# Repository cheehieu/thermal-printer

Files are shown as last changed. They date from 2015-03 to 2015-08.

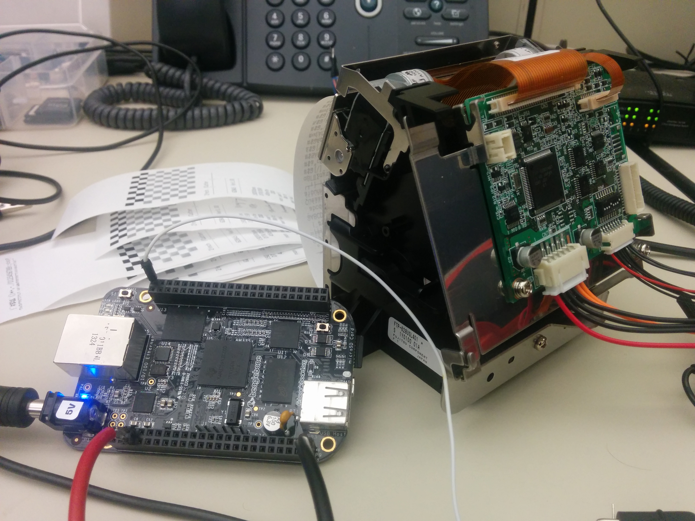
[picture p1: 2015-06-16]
images/printer_prototype.jpg

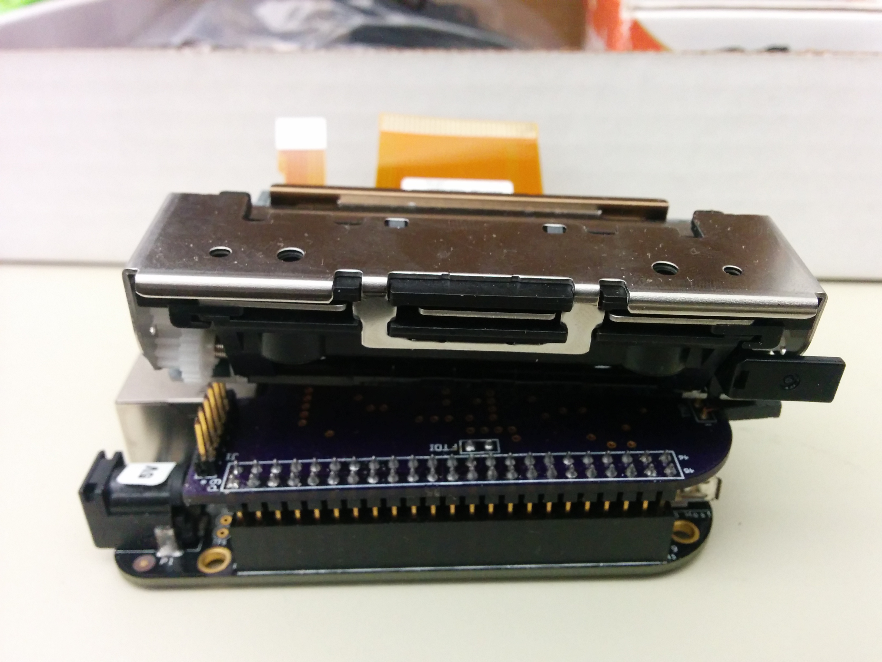
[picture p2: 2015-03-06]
images/print_head.jpg

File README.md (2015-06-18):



## Overview
This project is a thermal printer reference design featuring the PRU-ICSS on the AM335x. It was inspired by a similar project by [Andreas Dannenberg](https://gitorious.design.ti.com/pruprinter), who prototyped a functioning thermal printer out of a gutted POS unit and a BeagleBone Black. Here is a video of his prototype: [https://youtu.be/tVr5VrtNZiQ].

The main intent of this project is to showcase the real-time abilities of the PRU-ICSS for time-sensitive motor control applications. It also serves as a platform to demonstrate the new Linux-PRU software communication interface, . Much of this project's design follows Andreas' design choices (TI components, area- and cost-sensitive), but also incorporates some ideas from the FTP-628DSL491R interface board, which is an EVM for the Fujitsu FTP-628MCL401 print head.

## Hardware


### BeagleBone Black
The AM335x processor on the BeagleBone Black contains the Programmable Real-Time Unit and Industrial Communication Sub System (PRU-ICSS). The PRU consists of dual 32-bit RISC cores, which operate at 200MHz single cycle and have direct access to general IO. This allows for 100% predictable timing, making the PRU an excellent solution for thermal strobes and motor control. 

In this project, the PRU is designed to handle the print head logic and motor control for both head and cutter stepper motors. I tried to choose logical PRU signal groupings to simplify board layout and software design. Make sure to execute the proper pin-mux changes in the device tree. The PRU signals are connected on the cape as follows:

| BBB Pin |  PRU Signal | Cape Function |
|:---:|:---:|:---:|
| P8.30 | pru1_r30_11 | Vdd supply enable |
| P8.21 | pru1_r30_12 | VH supply enable |
| P8.20 | pru1_r30_13 | Buffer output enable |
| P8.15 | pru0_r31_15 | Motor driver fault HEAD |
| P9.26 | pru1_r31_16 | Motor driver fault CUT  |
| P8.46 | pru1_r30_1  | MTAn_head |
| P8.45 | pru1_r30_0  | MTA_head |
| P8.43 | pru1_r30_2  | MTBn_head |
| P8.44 | pru1_r30_3  | MTB_head |
| P8.41 | pru1_r30_4  | MTA_cut |
| P8.42 | pru1_r30_5  | MTAn_cut |
| P8.39 | pru1_r30_6  | MTB_cut |
| P8.40 | pru1_r30_7  | MTBn_cut |
| P9.31 | pru0_r30_0  | STB1 |
| P9.29 | pru0_r30_1  | STB2 |
| P9.30 | pru0_r30_2  | STB3 |
| P9.28 | pru0_r30_3  | STB4 |
| P9.42 | pru0_r30_4  | STB5 |
| P9.27 | pru0_r30_5  | STB6 |
| P8.12 | pru0_r30_14 | CLK |
| P9.41 | pru0_r30_6  | DI |
| P9.25 | pru0_r30_7  | LATn |
| P9.24 | pru0_r31_16 | DO |

Additional PRU information can be [here](http://processors.wiki.ti.com/index.php/PRU-ICSS), [here](http://elinux.org/Ti_AM33XX_PRUSSv2), and [here](http://www.element14.com/community/community/designcenter/single-board-computers/next-gen_beaglebone//blog/2013/05/22/bbb--working-with-the-pru-icssprussv2).

### Print Head


The star of this cape is the thermal print head: the [Fujitsu FTP-628MCL401](http://www.fujitsu.com/downloads/MICRO/fcai/thermal-printers/ftp-628mcl401.pdf). This print head is a high speed thermal printer featuring an auto cutter for full and partial paper cuts. It was selected by Paul Eaves after discussion with a Fujitsu FAE. Note that this is a different print head from Andreas' design. 

One important question that must be answered is the print head's pinout. The print head uses two FPC connectors; a 30-pin for the main print head and an 8-pin for the cutter. It is important to note that the pin assignments in the datasheet do not exactly match those connected on the interface board. I designed this cape using the datasheet pin outs, but it may become evident (during board bringup) to use the ones from the interface board. An "best guess" equivalent pin mapping is included in pru-printer/docs/TPCape_RevA_BOM.xlsx under the "interface" tab.

### Power
During operation, the FTP-628MCL401 print head draws a lot of current. The voltage and current specifications are listed below. In testing, it was possible to run the printer and interface board from the VDD_5V DC input on the BeagleBone Black using a 5VDC, 3A rated wall wart. However, it may have been drawing more than 3A to power the BBB and thermal printer EVM. So, a more robust solution was developed using a 12V supply input.

| Component  | Voltage (V) | Current (A) |
|---|---|---|
| Print head |  4.2 - 8.5  |  2.4 peak |
| Motor |  4.2 - 8.5  | 1.0 |
| Cutter | 4.75 - 8.5  | 1.0 |
| Logic |  3.0 - 5.25 | 0.1 |

I used WEBENCH to create a power solution for connecting a 12V, 5A wall wart (used with the X15). The power solution utilizes a TPS54332 for 12V to 7.2V (3A) conversion to supply VH to the print head. A TPS563209 is used for 12V to 5V (3A) conversion to supply the BeagleBone Black and subsequently the Vdd print head logic supply. These components were chosen for there low BOM cost/count, small footprint, and high efficiency. More details can be found at pru-printer/hw/docs/power/webench/

High side switches are used to control the VH and Vdd supplies. According to the datasheet, all lines connected to the head, including the power supply, must be set to "Low" in order to decrease power consumption during standby. An AND gate is used so that the VH supply will shut off in the event of a system reset.

### Motor Driver
Two DRV8833C motor drivers are utilized to drive the head and cutter stepper motors. This motor driver was selected for its protection features, output current capability, wide power supply voltage range, and its low cost. The PRU provides the control signal outputs.

### Print Sensors
The FTP-628MCL401 contains sensors for enabling additional features of the thermal printer. These include sensors for detecting an open platen, the temperature of the print head, the home position of the cutter, and the paper feed. Most of these sensors output an analog voltage to represent state. The printer datasheet recommends the usage of ADCs to monitor these voltages because they can be unstable.

However, this design utilizes LM393 comparators to trigger at specific threshold voltages created with voltage dividers. These comparators have open-collector outputs and can be wire-ANDed together to create a FAULTn error to the PRU.

### Misc.
Buffers are utilized to ensure signals are robust and can be tri-stated during reset or low-power operation. The SN74LVC244A buffers were selected for its low cost.

A hardware watchdog timer or voltage supervisor is used to ensure the STROBE signals are not active for too long, which would permanently damage the print head.

A standard cape EEPROM is included to store cape and pinmux information. This circuit is nearly identical to the one in the BeagleBone Black SRM. The difference being a fixed I2C address at 0x54, removing the need for a DIP switch.

An FTDI mating header is included to reroute the UART0 RX and TX signals to a more easily accessible connector.

Originally slated for the TPcape "Ultra" version, a Newhaven 2.4" touchscreen display is included for potentially more advanced print features.

### Connectors
The print head connectors used are the Molex 0526103072 (30-pin) and the Molex 0526100872 (8-pin).

## Software
No software is available yet. TI has since made considerable advances on the Linux-PRU front, but is may be useful to review the software work completed by Andreas. See pru-printer/sw/andreas_gitorious/ for the sources.

## Next Steps
* Finish PCB layout
* Order and assemble prototype components
* Board bringup
* Software development
* Implement more complex features like [cloud-connectivity](https://www.adafruit.com/products/1289)

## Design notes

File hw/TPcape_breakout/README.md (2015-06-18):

# Overview
This PCB is a breakout board to be used for prototyping a thermal printer with the BeagleBone Black. It utilizes 30-pin and 8-pin FPC connectors to interface with a Fujitsu FTP-628MCL401 print head. The breakout board breaks these print head signals out to standard 0.1" header pins, designated by "HEAD_OUT" and "CUT_OUT".

The board also contains a standard BeagleBone EEPROM for storing cape information and headers for accessing the FTDI serial RX/TX when the cape is mounted on a BBB. 

# Components
* 30-pin FPC connector; Molex 52610-3072
* 8-pin FPC connector; Molex 52610-0872
* 4-pin 2x2 surface mount female 0.1" header; Samtec SSM-102-S-DV
* 30-pin male 0.1" header for print head connector
* 8-pin male 0.1" header for cutter connector
* 5-pin male 0.1" header for USB-FTDI cable
* 2x26 0.1" header for BBB expansion (2)

* BBB cape EEPROM; CAT24C256WI-GT3
* 5.6k-ohm 0402 pull-up resistor (2)
* 4.75k-ohm 0402 pull-up resistor
* 0.1uF 0402 decoupling capacitor

# Gerbers
Gerbers and drill hole files are available in the "/Project Outputs..." directory. These design files have been uploaded to OSH Park and can be directly [purchased](https://oshpark.com/shared_projects/kP1HCuRb) for $31.15 (for 3 boards).

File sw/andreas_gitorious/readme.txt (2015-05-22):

//Repository lives at: https://gitorious.design.ti.com/pruprinter
//Video demonstration: https://youtu.be/tVr5VrtNZiQ

AM335x PRU-ICSS-based Thermal Printer Demo and Low-Level Driver
===============================================================
Copyright (C) 2014 Texas Instruments Incorporated - http://www.ti.com/
ALL RIGHTS RESERVED

Written by Andreas Dannenberg (dannenberg@ti.com)

Overview
--------
This project demonstrates how the AM335'x PRU-ICSS can be used to directly
drive and interface with a thermal printer assembly printing out bitmap
images. It comprises a low-level firmware that runs independently from the
main Linux CPU inside the PRU-ICSS and generates the neccessary signal waveforms
to drive the printer and a Linux command line application that reads PNG-
formatted monochrome bitmap images, processes them into a "print job", and
passes them to the low-level PRU-ICSS firmware for printing.

The software is designed such that it runs on a BeagleBone (white) EVM, with
all signals needed to interface with the printer assembly available on the
BeagleBone's P8 and P9 extension headers.

File System Organization
------------------------
demo_images/            Some PNG images that can be printed for demo purposes
doc/                    Various associated documentation/datasheets
kernel_support/         Kernel patch to configure the pinmux needed for PRU-ICSS
pcb/                    Hardware design information
src/                    Project source code folder
src/pruprint/           Linux host command-line application CCSv6.0 project
src/pruprinter_fw/      PRU-ICSS unit 1 low-level thermal printer driver
                        CCSv6.0 project.

Prerequisites
-------------
The project is based on TI's AM335x SDK 06_00_00_00 developer package and uses
the "Texas Instruments PRUSS driver" userspace I/O driver for communication with
the PRU-ICSS. Also, a small modification to the BSP source is needed to enable
the needed pinmix PRU-ICSS configuration during boot. In order to enable support
for this project the Kernel has to be build using the following steps:

(1) Enter the TI AM335x SDK root folder
$ cd ti-sdk-am335x-evm-06.00.00.00

(2) Apply the provided patch in the "kernel_support" folder to the Linux and BSP
tree
$ patch -p1 < <pruprinter-install-dir>/kernel_support/thermal-printer-bsp.patch

(3) Start the Kernel configuration and build process
$ make

Navigate to Device Drivers --> Userspace I/O drivers
Select the "Texas Instruments PRUSS  driver" to be build into the Kernel.
Select "Exit" to save the configuration and start building the new Kernel image.

(4) Copy/install the Kernel image into the appropriate location (SD-Card or NFS
folder)

Building the PRU Printer Project
--------------------------------
The project was developed and tested using the GA version of TI's Code
Composer Studio v6.0.0.00190 as well as version v2.0.0.B2 of TI's PRU-ICSS C
compiler obtained via the CCS app store. To build the project import and build
both 'pruprinter_fw' and 'pruprint' sub-projects into Code Composer. Note that
building the low-level firmware using 'pruprinter_fw' involves a custom build
step that requires the srec_cat tool to be installed in the system which is
part of the SRecord converter tool which can be installed by executing
'sudo apt-get install srecord' in the shell. Also note that the 'pruprinter_fw'
should be build as its output is consumed by 'pruprint'.

TODO
----
* Add more detailed documentation and code flow description
* Provide ready-to-use CCS debug configurations for easier debug session setup
* Create a Kernel patch that configures the PRU-ICSS signals used for the
  printer to safe defaults _before_ the pin mux configuration is changed to
  PRU-ICSS (to prevent potential erroneous and/or dangerous driving of the
  printer head/circuit)
* Optimize/verify signal timing based on the specific thermal printer assembly
  to be used

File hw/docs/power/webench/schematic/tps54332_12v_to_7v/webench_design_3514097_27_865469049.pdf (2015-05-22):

## WEBENCH ® Design Report

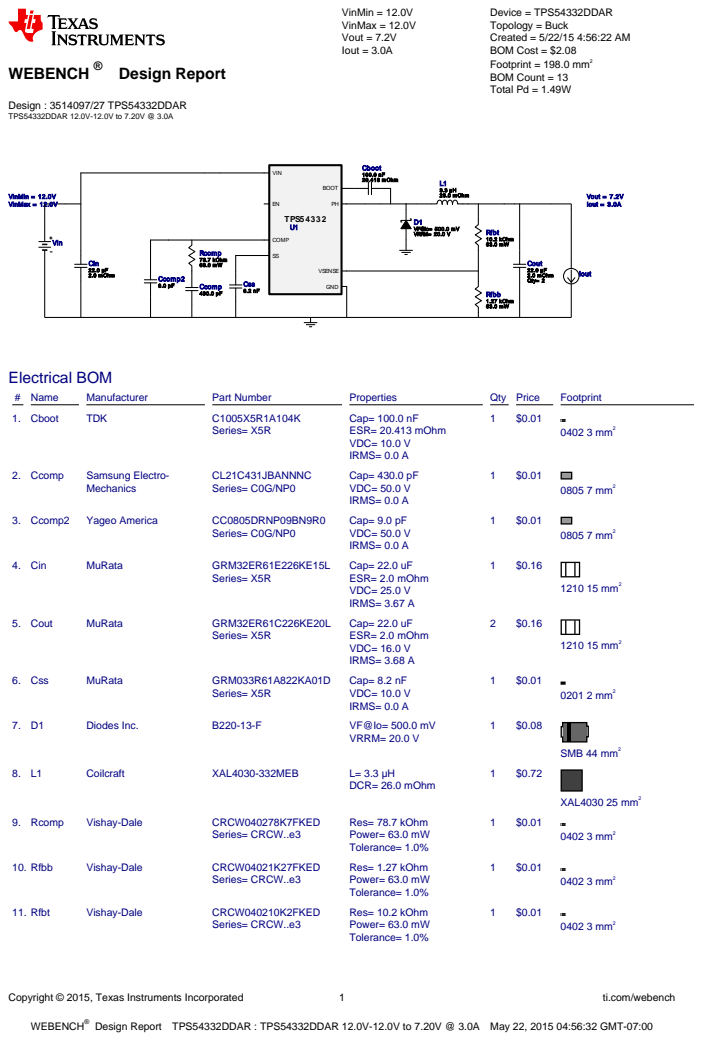
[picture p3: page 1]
Copyright © 2015, Texas Instruments Incorporated; ti.com/webench; WEBENCH®; Design : 3514097/27 TPS54332DDAR TPS54332DDAR 12.0V-12.0V to 7.20V @ 3.0A; VinMin = 12.0V VinMax = 12.0V Vout = 7.2V Iout = 3.0A; Device = TPS54332DDAR Topology = Buck Created = 5/22/15 4:56:22 AM BOM Cost = $2.08 Footprint = 198.0 mm² BOM Count = 13 Total Pd = 1.49W; Cboot 100.0 nF 20.413 mOhm; Ccomp 430.0 pF; Ccomp2 9.0 pF; Cin 22.0 µF 2.0 mOhm; Cout 22.0 µF 2.0 mOhm Qty= 2 Css; D1 VF@Io= 500.0 mV VRRM= 20.0 V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

Design Report TPS54332DDAR : TPS54332DDAR 12.0V-12.0V to 7.20V @ 3.0A May 22, 2015 04:56:32 GMT-07:00

Design

Copyright © 2015, Texas Instruments Incorporated | 2 | ti.com/webench
# Name | Manufacturer | Part Number | Properties | Qty Price | Footprint

12. U1 | Texas Instruments | TPS54332DDAR (http://www.ti.com/product/tps54332) | Switcher | 1 | $0.73

DDA0008H 57 mm²

IC Tj

Vin= 12.0V

0.25 | 0.50 | 0.75 | 1.00 | 1.25 | 1.50 | 1.75 | 2.00 | 2.25 | 2.50 | 2.75 | 3.00 Output Current (A)

35.0

37.5

40.0

42.5

45.0

47.5

50.0

52.5

55.0

57.5

60.0

62.5

65.0

67.5

70.0

IC Tj(degC)

Duty Cycle

Vin= 12.0V

0.25 | 0.50 | 0.75 | 1.00 | 1.25 | 1.50 | 1.75 | 2.00 | 2.25 | 2.50 | 2.75 | 3.00 Output Current (A)

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
Duty Cycle(%)

Cin IRMS

Vin= 12.0V

0.25 | 0.50 | 0.75 | 1.00 | 1.25 | 1.50 | 1.75 | 2.00 | 2.25 | 2.50 | 2.75 | 3.00 Output Current (A)

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
Cin IRMS(A)

IC Ipk

Vin= 12.0V

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

0.50

0.75

1.00

1.25

1.50

1.75

2.00

2.25

2.50

2.75

3.00

3.25

3.50

IC Ipk(A)

L Pd

Vin= 12.0V

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

0.000

0.025

0.050

0.075

0.100

0.125

0.150

0.175

0.200

0.225

0.250

L Pd(W)

Low Freq Gain

Vin= 12.0V

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

61.5

62.0

62.5

63.0

63.5

64.0

64.5

65.0

65.5

66.0

66.5

Low Freq Gain(dB)

Copyright © 2015, Texas Instruments Incorporated | 3 | ti.com/webench

D1 Tj

Vin= 12.0V

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
D1 Tj(degC)

Efficiency

Vin= 12.0V

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

92.25

92.50

92.75

93.00

93.25

93.50

93.75

94.00

94.25

94.50

94.75

Efficiency(%)

Vout p- p

Vin= 12.0V

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

0.00230

0.00235

0.00240

0.00245

0.00250

0.00255

0.00260

0.00265

0.00270

0.00275

0.00280

0.00285

0.00290

Vout p- p(V)

Cin Pd

Vin= 12.0V

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

0.00000

0.00025

0.00050

0.00075

0.00100

0.00125

0.00150

0.00175

0.00200

0.00225

0.00250

0.00275

0.00300

0.00325

0.00350

0.00375

0.00400

0.00425

Cin Pd(W)

Cout Pd

Vin= 12.0V

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

0.000055

0.000056

0.000057

0.000058

0.000059

0.000060

0.000061

0.000062

0.000063

0.000064

0.000065

0.000066

0.000067

0.000068

Cout Pd(W)

M Vds Act

Vin= 12.0V

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

0.00

0.01

0.02

0.03

0.04

0.05

0.06

0.07

0.08

0.09

0.10

0.11

0.12

0.13

0.14

0.15

M Vds Act(V)

Copyright © 2015, Texas Instruments Incorporated | 4 | ti.com/webench

M Irms

Vin= 12.0V

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

0.50

0.75

1.00

1.25

1.50

1.75

2.00

2.25

M Irms(A)

Pout

Vin= 12.0V

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

2.5

5.0

7.5

10.0

12.5

15.0

17.5

20.0

22.5

Pout(W)

Iin Avg

Vin= 12.0V

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
Iin Avg(A)

Total Pd

Vin= 12.0V

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
Total Pd(W)

Cout IRMS

Vin= 12.0V

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

0.2350

0.2375

0.2400

0.2425

0.2450

0.2475

0.2500

0.2525

0.2550

0.2575

0.2600

Cout IRMS(A)

L Ipp

Vin= 12.0V

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

0.72

0.73

0.74

0.75

0.76

0.77

0.78

0.79

0.80

0.81

0.82

0.83

0.84

0.85

0.86

0.87

0.88

0.89

0.90

0.91

L Ipp(A)

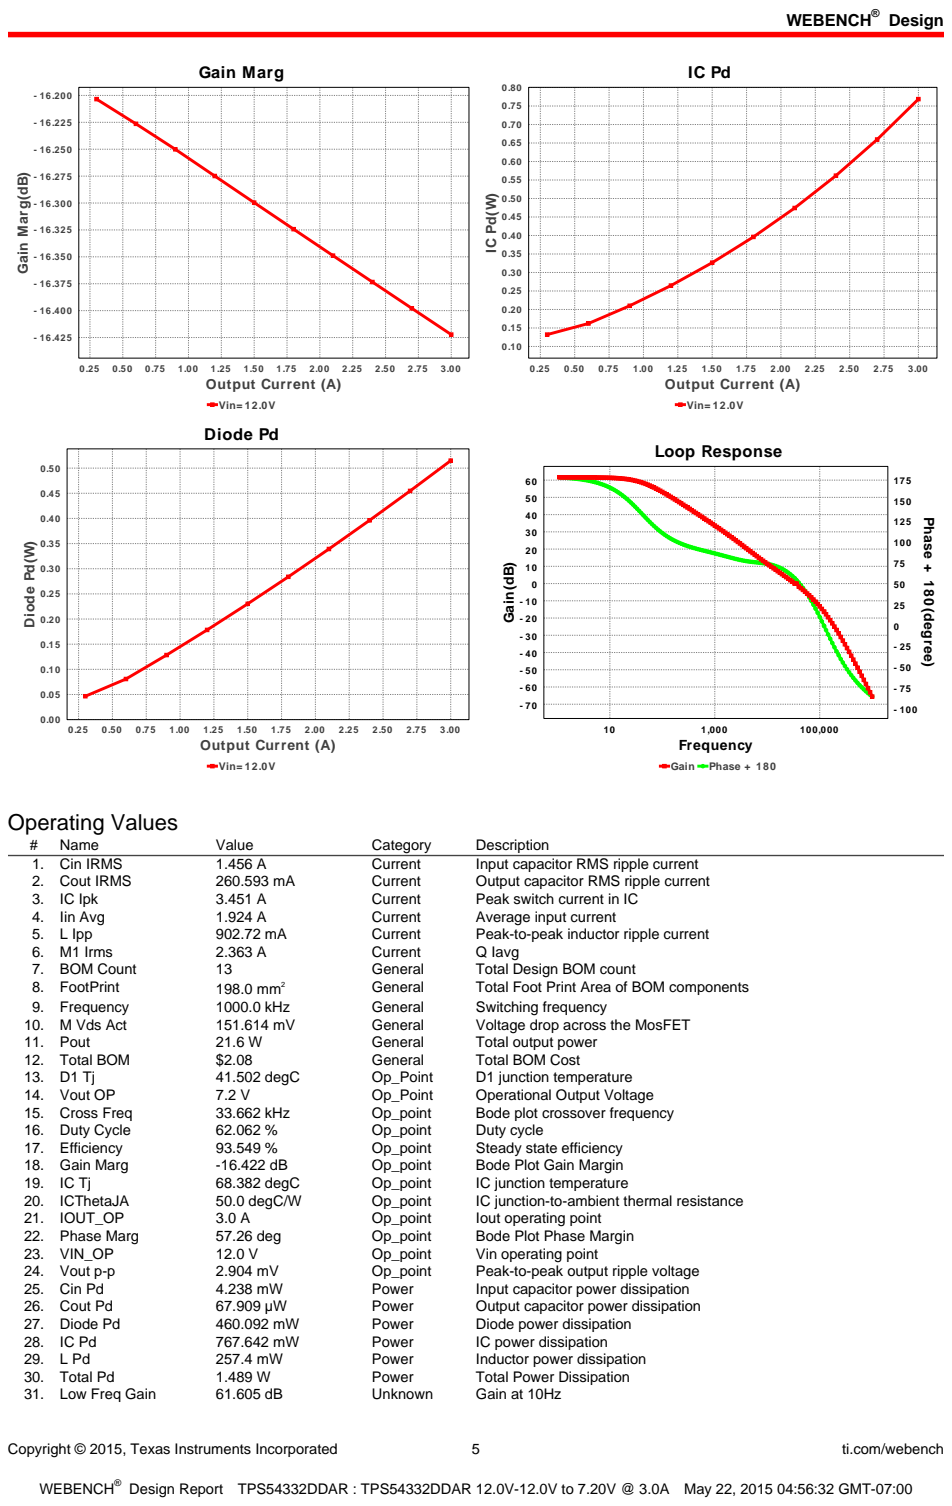
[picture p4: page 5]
Copyright © 2015, Texas Instruments Incorporated; ti.com/webench; Gain Marg; Vin= 12.0V; 0.25 0.50 0.75 1.00 1.25 1.50 1.75 2.00 2.25 2.50 2.75 3.00 Output Current (A); 3.00 Output Current (A); Diode Pd; Diode Pd(W); Loop Response; Gain Phase + 180; 100,000 Frequency; Gain(dB); Phase + 180(degree); Operating Values; Name; Value; Category; Description; 1. Cin IRMS; Current; Input capacitor RMS ripple current; 2. Cout IRMS; Output capacitor RMS ripple current; 3. IC Ipk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

Gain Marg(dB)

Copyright © 2015, Texas Instruments Incorporated | 6 | ti.com/webench

## Design Inputs

# | Name | Value | Description

1. Iout | 3.0 | Maximum Output Current
2. Iout1 | 3.0 | Output Current #1
3. VinMax | 12.0 | Maximum input voltage
4. VinMin | 12.0 | Minimum input voltage
5. Vout | 7.2 | Output Voltage
6. Vout1 | 7.2 | Output Voltage #1
7. base_pn | TPS54332 | Base Product Number
8. source | DC | Input Source Type
9. Ta | 30.0 | Ambient temperature

## Design Assistance

1. TPS54332 Product Folder : http://www.ti.com/product/tps54332 : contains the data sheet and other resources.

Texas Instruments' WEBENCH simulation tools attempt to recreate the performance of a substantially equivalent physical implementation
of the design. Simulations are created using Texas Instruments' published specifications as well as the published specifications of other device manufacturers. While Texas Instruments does update this information periodically, this information may not be current at the time the simulation is built. Texas Instruments does not warrant the accuracy or completeness of the specifications or any information contained therein. Texas Instruments does not warrant that any designs or recommended parts will meet the specifications you entered, will be suitable for your application or fit for any particular purpose, or will operate as shown in the simulation in a physical implementation. Texas Instruments does not warrant that the designs are production worthy.
You should completely validate and test your design implementation to confirm the system functionality for your application prior to production.
Use of Texas Instruments' WEBENCH simulation tools is subject to Texas Instruments' Site Terms and Conditions of Use. (http://www.ti.com/corp/docs/legal/termsofuse.shtml) Prototype boards based on WEBENCH created designs are provided AS IS without warranty of any kind for evaluation and testing purposes and are subject to the terms of the Evaluation License Agreement. (http://www.ti.com/corp/docs/legal/termsofuse_estore.shtml)

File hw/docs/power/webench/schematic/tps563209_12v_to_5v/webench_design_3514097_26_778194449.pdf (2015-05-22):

## WEBENCH ® Design Report

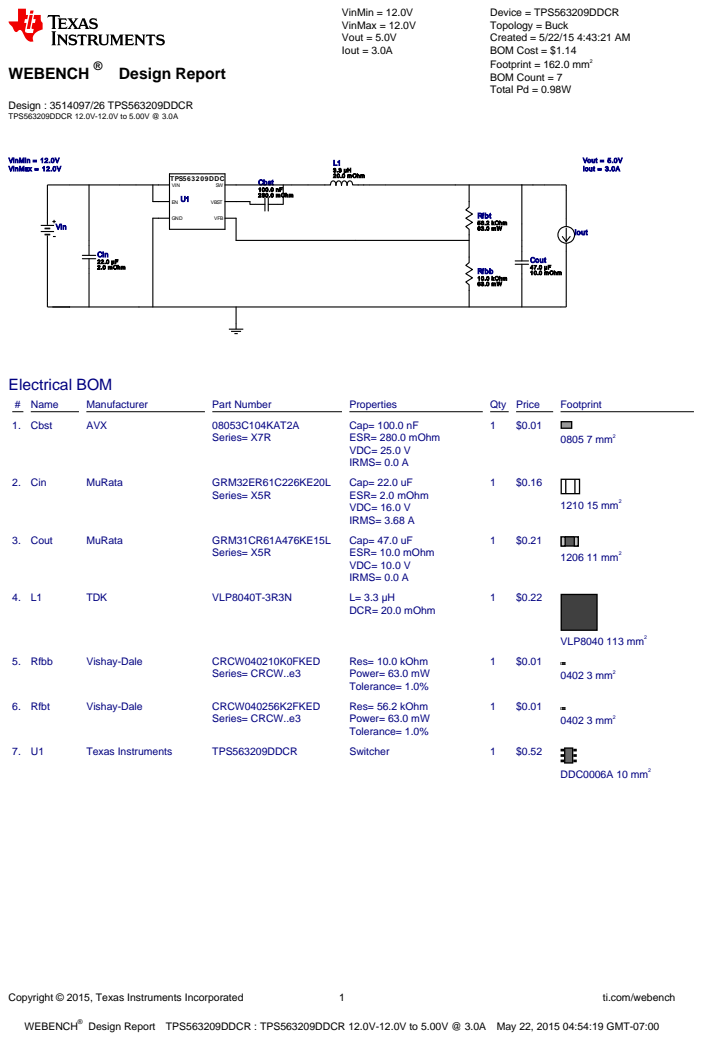
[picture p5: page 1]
Copyright © 2015, Texas Instruments Incorporated; ti.com/webench; WEBENCH®; Design : 3514097/26 TPS563209DDCR TPS563209DDCR 12.0V-12.0V to 5.00V @ 3.0A; VinMin = 12.0V VinMax = 12.0V Vout = 5.0V Iout = 3.0A; Device = TPS563209DDCR Topology = Buck Created = 5/22/15 4:43:21 AM BOM Cost = $1.14 Footprint = 162.0 mm² BOM Count = 7 Total Pd = 0.98W; Cbst 100.0 nF 280.0 mOhm; Cin 22.0 µF 2.0 mOhm; Cout 47.0 µF 10.0 mOhm; L1 3.3 µH 20.0 mOhm; Rfbb 10.0 kOhm 63.0 mW; Rfbt 56.2 kOhm 63.0 mW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

Design Report TPS563209DDCR : TPS563209DDCR 12.0V-12.0V to 5.00V @ 3.0A May 22, 2015 04:54:19 GMT-07:00

Design

Copyright © 2015, Texas Instruments Incorporated | 2 | ti.com/webench

L Ipp

Vin= 12.0V

0.00 0.25 0.50 0.75 1.00 1.25 1.50 1.75 2.00 2.25 2.50 2.75 3.00 Output Current (A)

1.1025

1.1050

1.1075

1.1100

1.1125

1.1150

1.1175

1.1200

1.1225

1.1250

L Ipp(A)

Vout p- p

Vin= 12.0V

0.00 0.25 0.50 0.75 1.00 1.25 1.50 1.75 2.00 2.25 2.50 2.75 3.00 Output Current (A)

- 0.0275
- 0.0250
- 0.0225
- 0.0200
- 0.0175
- 0.0150
- 0.0125
- 0.0100
- 0.0075
- 0.0050
- 0.0025

0.0000

0.0025

0.0050

0.0075

0.0100

0.0125

0.0150

Vout p- p(V)

Duty Cycle

Vin= 12.0V

0.00 0.25 0.50 0.75 1.00 1.25 1.50 1.75 2.00 2.25 2.50 2.75 3.00 Output Current (A)

41.6

41.7

41.8

41.9

42.0

42.1

42.2

42.3

42.4

42.5

42.6

42.7

42.8

42.9

43.0

43.1

43.2

Duty Cycle(%)

Efficiency

Vin= 12.0V

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
Efficiency(%)

IC Tj

Vin= 12.0V

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

35.0

37.5

40.0

42.5

45.0

47.5

50.0

52.5

55.0

57.5

60.0

62.5

65.0

67.5

70.0

72.5

75.0

77.5

80.0

IC Tj(degC)

Cin Pd

Vin= 12.0V

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

0.00000

0.00025

0.00050

0.00075

0.00100

0.00125

0.00150

0.00175

0.00200

0.00225

0.00250

0.00275

0.00300

0.00325

0.00350

0.00375

0.00400

0.00425

0.00450

Cin Pd(W)

Copyright © 2015, Texas Instruments Incorporated | 3 | ti.com/webench

Cin IRMS

Vin= 12.0V

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
Cin IRMS(A)

Iin Avg

Vin= 12.0V

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
Iin Avg(A)

Pout

Vin= 12.0V

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
Pout(W)

Cout IRMS

Vin= 12.0V

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

0.3180

0.3185

0.3190

0.3195

0.3200

0.3205

0.3210

0.3215

0.3220

0.3225

0.3230

0.3235

0.3240

0.3245

0.3250

Cout IRMS(A)

Cout Pd

Vin= 12.0V

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

0.0010125

0.0010150

0.0010175

0.0010200

0.0010225

0.0010250

0.0010275

0.0010300

0.0010325

0.0010350

0.0010375

0.0010400

0.0010425

0.0010450

0.0010475

0.0010500

0.0010525

0.0010550

Cout Pd(W)

Total Pd

Vin= 12.0V

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

0.00

0.05

0.10

0.15

0.20

0.25

0.30

0.35

0.40

0.45

0.50

0.55

0.60

0.65

0.70

0.75

0.80

0.85

0.90

0.95

1.00

Total Pd(W)

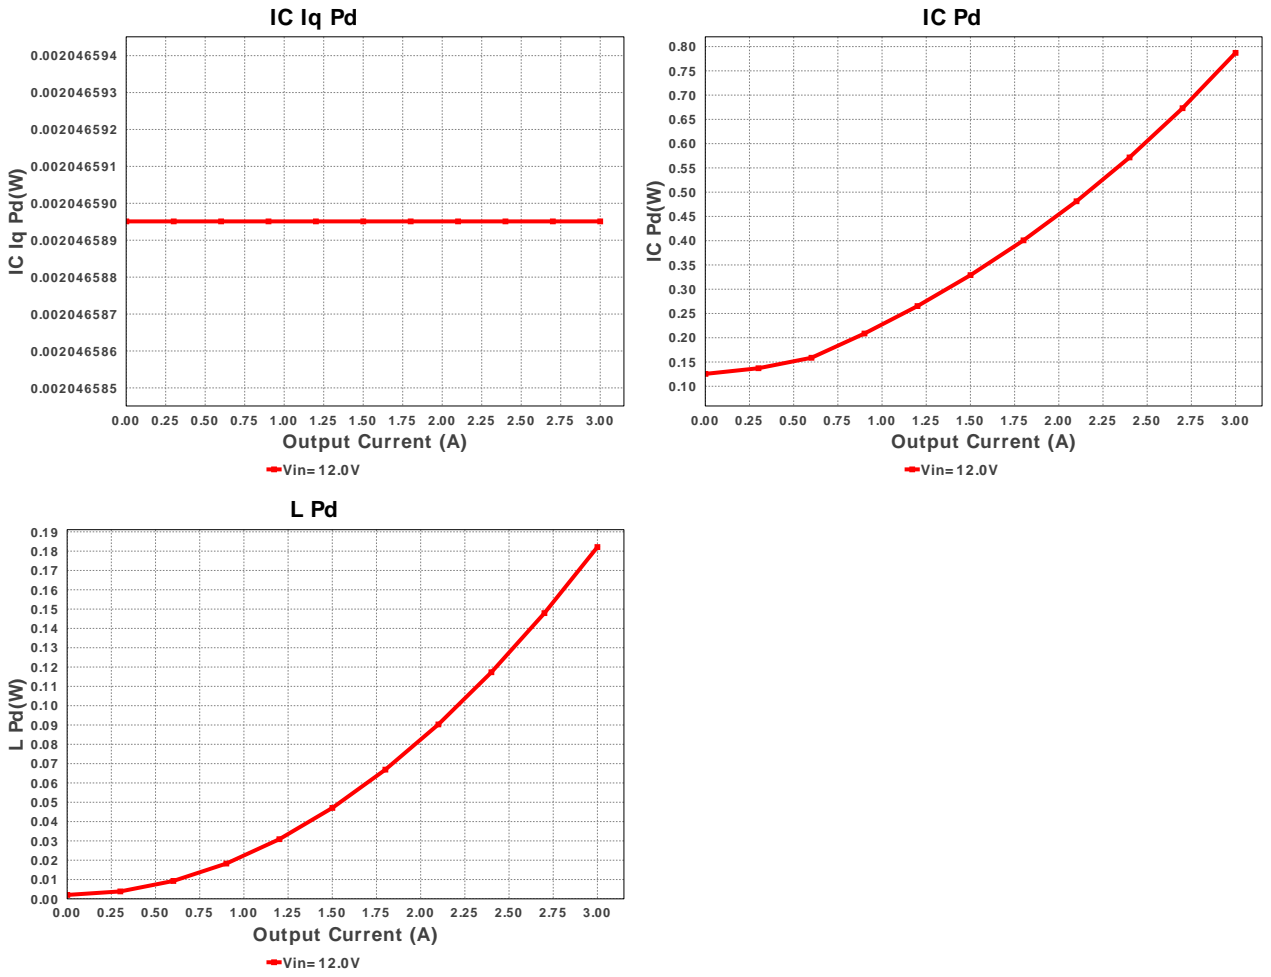
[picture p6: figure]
Vin= 12.0V

Copyright © 2015, Texas Instruments Incorporated | 4 | ti.com/webench

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

## Operating Values

# | Name | Value | Category | Description

1. Cin IRMS | 1.501 A | Current | Input capacitor RMS ripple current
2. Cout IRMS | 324.699 mA | Current | Output capacitor RMS ripple current
3. Iin Avg | 1.331 A | Current | Average input current
4. L Ipp | 1.125 A | Current | Peak-to-peak inductor ripple current
5. BOM Count | 7 | General | Total Design BOM count
6. FootPrint | 162.0 mm² | General | Total Foot Print Area of BOM components
7. Frequency | 790.897 kHz | General | Switching frequency
8. Pout | 15.0 W | General | Total output power
9. Total BOM | $1.14 | General | Total BOM Cost
10. Vout OP | 5.0 V | Op_Point | Operational Output Voltage
11. Duty Cycle | 43.168 % | Op_point | Duty cycle
12. Efficiency | 93.896 % | Op_point | Steady state efficiency
13. IC Tj | 79.507 degC | Op_point | IC junction temperature
14. ICThetaJA | 62.9 degC/W | Op_point | IC junction-to-ambient thermal resistance
15. IOUT_OP | 3.0 A | Op_point | Iout operating point
16. VIN_OP | 12.0 V | Op_point | Vin operating point
17. Vout p-p | 11.248 mV | Op_point | Peak-to-peak output ripple voltage
18. Cin Pd | 4.507 mW | Power | Input capacitor power dissipation
19. Cout Pd | 1.054 mW | Power | Output capacitor power dissipation
20. IC Iq Pd | 2.047 mW | Power | IC Iq Pd
21. IC Pd | 787.073 mW | Power | IC power dissipation
22. L Pd | 182.109 mW | Power | Inductor power dissipation
23. Total Pd | 975.151 mW | Power | Total Power Dissipation

## Design Inputs

# | Name | Value | Description

1. Iout | 3.0 | Maximum Output Current
2. Iout1 | 3.0 | Output Current #1
3. VinMax | 12.0 | Maximum input voltage
4. VinMin | 12.0 | Minimum input voltage

Copyright © 2015, Texas Instruments Incorporated | 5 | ti.com/webench
# | Name | Value | Description

5. Vout | 5.0 | Output Voltage
6. Vout1 | 5.0 | Output Voltage #1
7. base_pn | TPS563209 | Base Product Number
8. source | DC | Input Source Type
9. Ta | 30.0 | Ambient temperature

## Design Assistance

1. TPS563209 Product Folder : http://www.ti.com/lit/ds/symlink/tps563209.pdf : contains the data sheet and other resources.

Texas Instruments' WEBENCH simulation tools attempt to recreate the performance of a substantially equivalent physical implementation
of the design. Simulations are created using Texas Instruments' published specifications as well as the published specifications of other device manufacturers. While Texas Instruments does update this information periodically, this information may not be current at the time the simulation is built. Texas Instruments does not warrant the accuracy or completeness of the specifications or any information contained therein. Texas Instruments does not warrant that any designs or recommended parts will meet the specifications you entered, will be suitable for your application or fit for any particular purpose, or will operate as shown in the simulation in a physical implementation. Texas Instruments does not warrant that the designs are production worthy.
You should completely validate and test your design implementation to confirm the system functionality for your application prior to production.
Use of Texas Instruments' WEBENCH simulation tools is subject to Texas Instruments' Site Terms and Conditions of Use. (http://www.ti.com/corp/docs/legal/termsofuse.shtml) Prototype boards based on WEBENCH created designs are provided AS IS without warranty of any kind for evaluation and testing purposes and are subject to the terms of the Evaluation License Agreement. (http://www.ti.com/corp/docs/legal/termsofuse_estore.shtml)

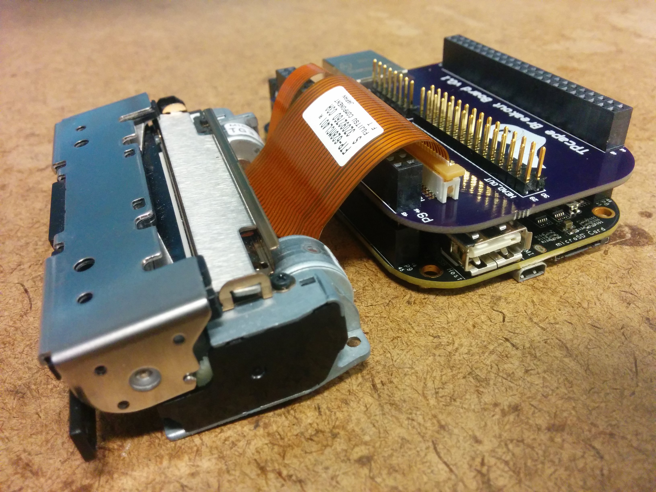
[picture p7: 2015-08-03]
images/TPcape_breakout_connect_side.jpg

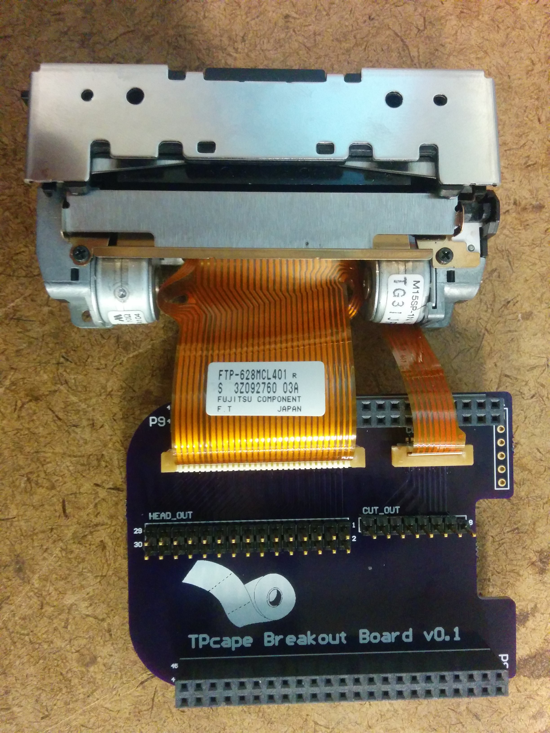
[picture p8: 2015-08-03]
images/TPcape_breakout_connect_top.jpg

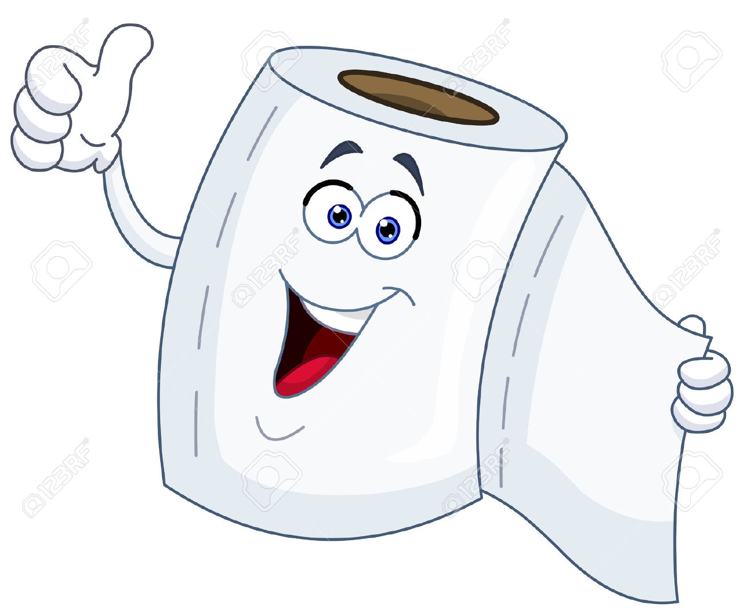
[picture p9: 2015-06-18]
hw/docs/silk/thumbs.jpg

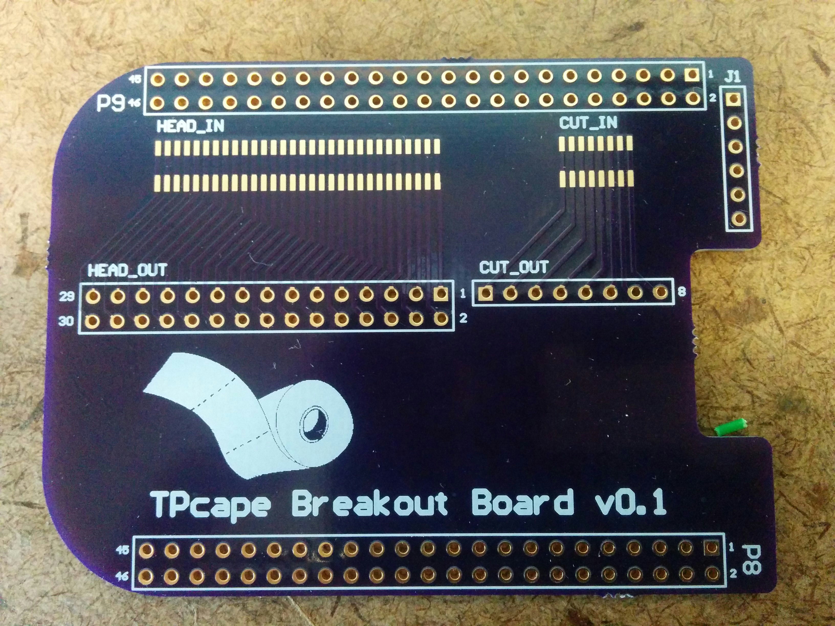
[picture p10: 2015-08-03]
images/TPcape_breakout_fab.jpg

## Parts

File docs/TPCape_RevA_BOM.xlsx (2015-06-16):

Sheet: TPcape_BOM
 |  |  |  |  | Capture CIS Standard Bill Of Materials - Standard Report
 |  |  |  |  |  | Report Created on Tuesday Feb 03 06:18:09 2015
Final
Doc = am572x_industrial_evm_3M0001.dsn
RevCode = 1.1A
Title = AM572X Industrial EVM
ITEM | QTY | REFERENCE DESIGNATOR | VALUE | DESCRIPTION | MFR | MFR PART # | TI INT PART # | VENDOR | VENDOR PART # | UNIT COST | QTY COST | COMMENTS
1 | 1 | TPCape |  | PCB 3.5"x2.5", 2-layer | OSH Park |  |  | OSH Park |  |  | $0.00
2 | 1 |  |  | Fujitsu Mechanism, 2-inch ELM with low profile cutter | Fujitsu | FTP-628MCL401 |  | Mouser |  |  | $0.00
3 | 1 | FFC_HEAD | 30-pin | CONN FPC VERT 30POS 1.00MM SMD | Molex Inc | 0526103072 |  | Digi-Key | WM6765CT-ND (http://www.digikey.com/product-detail/en/0526103072/WM6765CT-ND/3044179) | $2.90 | $2.90 | FFC connector for print head
4 | 1 | FFC_CUT | 8-pin | CONN FPC VERT 8POS 1.00MM SMD | Molex Inc | 0526100872 |  | Digi-Key | WM6761CT-ND (http://www.digikey.com/product-detail/en/0526100872/WM6761CT-ND/3044175) | $0.93 | $0.93 | FFC connector for print cutter
5 | 1 | FTDI | 4-pin | 0.1" recepticle, surface mount, gold | Samtec | SSM-102-S-DV |  |  |  |  | $0.00
6 | 1 | LCD | 40-pin | CONN FFC BOTTOM 40POS 0.50MM R/A | Molex Inc | 541324062 |  | Digi-Key | WM3436CT-ND (http://www.digikey.com/product-detail/en/0541324062/WM3436CT-ND/2405614) | $2.26 | $2.26 | FFC connector for New Haven TFT display
7 | 1 | PRINT |  | Tactile switch for PRINT feature |  |  |  |  |  |  | $0.00
8 |  |  |  | Capacitor Ceramic 4.7uF 16V 10% 0603 | Taiyo Yuden | EMK107ABJ475KA-T |  |  |  |  | $0.00
9 |  |  |  | Capacitor 1uF 10V Ceramic 10% 0402 | AVX | 0402ZD105KAT2A |  |  |  |  | $0.00
10 |  |  |  | NPN transistor | Diodes Inc | MMBT2222A |  | Digi-Key | MMBT2222A-FDICT-ND (http://www.digikey.com/product-detail/en/MMBT2222A-7-F/MMBT2222A-FDICT-ND/815723) | $0.14 | $0.00
11 | 1 |  |  | IC EEPROM 256KBIT 400KHZ 8SOIC | ON Semi | CAT24C256WI-GT3 (https://www.onsemi.com/PowerSolutions/product.do?id=CAT24C256WI-GT3) |  | Digi-Key | CAT24C256WI-GT3OSCT-ND (http://www.digikey.com/product-detail/en/CAT24C256WI-GT3/CAT24C256WI-GT3OSCT-ND/2704982) | $0.73 | $0.73
12 |  |  |  |  |  |  |  |  |  |  | $0.00
13 |  |  |  |  |  |  |  |  |  |  | $0.00
14 |  |  |  |  |  |  |  |  |  |  | $0.00
15 |  |  |  |  |  |  |  |  |  |  | $0.00
16 |  |  |  |  |  |  |  |  |  |  | $0.00
17 |  | CA1, CA2, CA3 | 1000pF | CAP ARRAY 1000PF 100V X7R 1206 |  | GNM314B11H102KD01D |  |  |  |  | $0.00
18 |  | C1, C2 | 47uF | Aluminum electrolytic cap, 16V, 20%, 6.3x5.4 | Nichicon | UWT1C470MBL1GB |  |  |  |  | $0.00
19 |  | C30, C32, C58, C59 | 2200pF | 0402, 50Vdc, | Murata | GRM155B11H222KA01 |  |  |  |  | $0.00
20 |  | C31, C33, C34 | 0.1uF | 0402, 16Vdc, | Murata | GRM155F11C104ZA01 |  |  |  |  | $0.00
21 |  | C36, C37, C40 | 47pF | 0402, 50Vdc, 0+/-60ppm/C | Murata | GRM1552C1H470JZ01 |  |  |  |  | $0.00
22 |  |  |  |  |  |  |  |  |  |  | $0.00
23 |  | R15 | 12 | 0805, 5%, | Rohm | MCR10HJ120 |  |  |  |  | $0.00
24 |  | R28 | 10K | Surface Mount Thick Film Chip Resistor 0402 Case 10K Ohms 1% Tolerance 100 PPM | Rohm | MCR01MZSF1002 |  |  |  |  | $0.00
25 |  | R31 | 1K | 0402, 5%, | Rohm | MCR01HJ102
26 |  | R32 | 4.7K | 0402, 5% | Rohm | MCR01HJ472
27 |  | R33, R63 | 15K | Surface Mount Thick Film Chip Resistor 0402 Case 15K Ohms 1% Tolerance 100 PPM | Rohm | MCR01MZSF1502
28 |  | R35, R64 | 180 | 0805, 5%, | Rohm | MCR10HJ181
29 |  | RA17, RA21, RA23a, RA24 | 22K | RES ARRAY 22K OHM 4 RES 1206 | Rohm | MNR14E0ABJ223
30
31 |  | Q7 |  |  |  | DTC124EUA
32
33
34
25 | 246 | C3 C7 C8 C9 C10 C11 C12 C14 C15 C16 C17 C28 C29 C30 C31 C32 C34 C35 C36 C37 C38 C39 C40 C41 C42 C43 C48 C49 C50 C51 C55 C56 C57 C58 C59 C60 C61 C62 C63 C65 C66 C67 C68 C69 C70 C71 C72 C73 C74 C75 C76 C77 C78 C79 C81 C105 C112 C113 C114 C115 C118 C120 C127 C130 C137 C139 C142 C144 C151 C152 C165 C169 C170 C171 C186 C190 C191 C192 C195 C207 C210 C214 C216 C219 C220 C221 C225 C226 C227 C228 C229 C230 C232 C233 C234 C235 C236 C238 C239 C240 C242 C248 C251 C255 C256 C257 C258 C261 C262 C263 C264 C267 C308 C309 C310 C315 C319 C321 C322 C324 C326 C327 C328 C329 C330 C331 C332 C334 C335 C336 C337 C338 C339 C341 C342 C343 C344 C345 C346 C348 C349 C351 C352 C353 C355 C356 C357 C358 C359 C360 C362 C363 C364 C365 C366 C367 C368 C369 C370 C371 C372 C373 C374 C376 C377 C378 C379 C380 C381 C385 C386 C388 C389 C390 C391 C393 C394 C397 C398 C400 C401 C403 C404 C405 C406 C408 C409 C410 C420 C422 C423 C424 C425 C426 C427 C428 C429 C430 C443 C444 C448 C451 C453 C469 C470 C480 C481 C482 C485 C486 C487 C488 C489 C490 C491 C493 C494 C495 C496 C497 C498 C499 C500 C501 C502 C506 C507 C508 C509 C511 C512 C513 C514 C515 C516 C517 C518 C519 C520 C524 C547 C548 C550 C551 C552 C553 | 0.01uF | Capacitor 0.01uF 16V 10% 0402 | Kemet | C0402C103K4RACTU | 1C0012 | Digikey | 311-1101-2-ND (http://www.digikey.com/product-detail/en/CC0805JRNPO9BN150/311-1101-2-ND/302835) |  | #REF!

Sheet: Connectors
FPC for FTP-628MCL401
Pin | Signal | I/O | BBB Pin | BBB Signal | Detail
1 | PHK | - | - | - | Photo interruptor cathode |  | Current limiting resistor for IF = 20mA (165-ohm for 3.3V, 90-ohm for 1.8V, 250-ohm for 5V)
2 | VSEN | I | P9.4 | VDD_3V3 | Paper sensor power |  | 1.8V for ADC? MOSFET to control for standby
3 | PHE | O |  |  | Photo interruptor emitter |  | Emitter resistor to GND, output to ADC?
4 | VH | I | P9.6 | VDD_5V | Head drive power |  | P8.11 | pru0_r30_15 | MMC1_CLK
5 | VH | I | P9.6 | VDD_5V | Head drive power |  | P8.16 | pru0_r31_14 | MMC1_CMD
6 | DI | I | P9.41 | pru0_r30_6 | Data in
7 | CLK | I | P8.12 | pru0_r30_14 | Clock |  | BBB Pin | PRU Signal | Cape Signal
8 | GND | - | - | DGND | Head ground | LCD_AC_BIAS_EN | P8.30 | pru1_r30_11 | Vdd supply enable
9 | GND | - | - | DGND | Head ground |  | P8.21 | pru1_r30_12 | VH supply enable
10 | STB6 | I | P9.27 | pru0_r30_5 | Strobe 6 |  | P8.20 | pru1_r30_13 | Buffer output enable
11 | STB5 | I | P9.42 | pru0_r30_4 | Strobe 5 |  | P8.15 | pru0_r31_15 | Motor driver fault HEAD
12 | STB4 | I | P9.28 | pru0_r30_3 | Strobe 4 |  | P9.26 | pru1_r31_16 | Motor driver fault CUT
13 | VDD | I | P9.4 | VDD_3V3 | Logic power |  | P8.46 | pru1_r30_1 | MTAn_head
14 | TM | O |  |  | Thermistor |  | P8.45 | pru1_r30_0 | MTA_head
15 | TM | O |  |  | Thermistor |  | P8.43 | pru1_r30_2 | MTBn_head
16 | STB3 | I | P9.30 | pru0_r30_2 | Strobe 3 |  | P8.44 | pru1_r30_3 | MTB_head
17 | STB2 | I | P9.29 | pru0_r30_1 | Strobe 2 |  | P8.41 | pru1_r30_4 | MTA_cut
18 | STB1 | I | P9.31 | pru0_r30_0 | Strobe 1 |  | P8.42 | pru1_r30_5 | MTAn_cut
19 | GND | - | - | DGND | Head ground |  | P8.39 | pru1_r30_6 | MTB_cut
20 | GND | - | - | DGND | Head ground |  | P8.40 | pru1_r30_7 | MTBn_cut
21 | LATn | I | P9.25 | pru0_r30_7 | Data latch |  | P9.31 | pru0_r30_0 | STB1
22 | DO | O | P9.24 | pru0_r31_16 | Data out |  | P9.29 | pru0_r30_1 | STB2
23 | VH | I | P9.6 | VDD_5V | Head drive power |  | P9.30 | pru0_r30_2 | STB3
24 | VH | I | P9.6 | VDD_5V | Head drive power |  | P9.28 | pru0_r30_3 | STB4
25 | SWn | I |  |  | Platen release switch |  | P9.42 | pru0_r30_4 | STB5
26 | SW | O |  |  | Platen release switch |  | P9.27 | pru0_r30_5 | STB6
27 | MTAn | I | P8.46 | pru1_r30_1 | Head motor excitation signal An |  | P8.12 | pru0_r30_14 | CLK
28 | MTA | I | P8.45 | pru1_r30_0 | Head motor excitation signal A |  | P9.41 | pru0_r30_6 | DI
29 | MTBn | I | P8.43 | pru1_r30_2 | Head motor excitation signal Bn |  | P9.25 | pru0_r30_7 | LATn
30 | MTB | I | P8.44 | pru1_r30_3 | Head motor excitation signal B |  | P9.24 | pru0_r31_16 | DO
1 | VSEN | I | P9.4 | VDD_3V3 | Home position sensor power |  | Same as VSEN pin2 above
2 | PHE | O |  |  | Photo interruptor emitter |  | Emitter resistor to GND, output to ADC?
3 | PHK | - | - | - | Photo interruptor cathode |  | Current limiting resistor for IF = 20mA (165-ohm for 3.3V, 90-ohm for 1.8V, 250-ohm for 5V)
4 | MTA | I | P8.41 | pru1_r30_4 | Cutter motor excitation signal A
5 | MTAn | I | P8.42 | pru1_r30_5 | Cutter motor excitation signal An
6 | MTB | I | P8.39 | pru1_r30_6 | Cutter motor excitation signal B
7 | MTBn | I | P8.40 | pru1_r30_7 | Cutter motor excitation signal Bn
8 | NC | -
6 | strobes |  |  | output
3 | head signals |  |  | output
4 | head motor |  |  | output
4 | cutter motor |  |  | output
1 | head signal |  |  | input
2 | nfault |  |  | input
2 | power control |  |  | output
1 | output enable |  |  | output
20

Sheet: interface
TPcape |  |  | Translation? |  |  | Interface board
Pin | Signal | I/O | Pin | Signal | I/O | Pin | Signal | I/O | Detail
1 | PHK | - | 1 | R35 | - | 1 | R35 | - | MCR10HJ181
2 | VSEN | I | 2 | Vcc2 | I | 2 | Vcc2 | I | C33 (GRM155F11C104ZA01) decap to AGND, MOSFET controlled by /SRD | ~1.46V (PWM @ 5V) at standby. 5V running
3 | PHE | O | 3 | /PES | O | 3 | /PES | O | R33 (MCR01MZSF1502) emitter resistor to GND, C30 (GRM155B11H222KA01) decap, C37 (GRM1552C1H470JZ01) decap at MCU input, | Outputs 0 if no paper. Outputs ~0.85V (PWM @ 5V) if paper detected, or 5V when running
4 | VH | I | 6 | VH | I | 4 | HUP | O | R31 (MCR01HJ102), R32 (MCR01HJ472), CA2 (GNM314B11H102KD01D) chatter prevention
5 | VH | I | 7 | VH | I | 5 | Vlog | I | C31 (GRM155F11C104ZA01) decap to AGND, MOSFET controlled by /HON, C2 at CN7 input
6 | DI | I | 8 | HDO | I | 6 | VH | I | C34 (GRM155F11C104ZA01) decap to AGND
7 | CLK | I | 9 | HCLK | I | 7 | VH | I
8 | GND | - | 10 | GND | - | 8 | HDO | I | RA21 (MNR14E0ABJ223), CA3 (GNM314B11H102KD01D)
9 | GND | - | 11 | GND | - | 9 | HCLK | I | RA21 (MNR14E0ABJ223), CA3 (GNM314B11H102KD01D)
10 | STB6 | I | 12 | STB6 | I | 10 | GND | - | Connect to AGND
11 | STB5 | I | 13 | STB5 | I | 11 | GND | - | Connect to AGND
12 | STB4 | I | 14 | STB4 | I | 12 | STB6 | I | RA24 (MNR14E0ABJ223), CA2 (GNM314B11H102KD01D)
13 | VDD | I | 15 | Vlog | I | 13 | STB5 | I | RA24 (MNR14E0ABJ223), CA2 (GNM314B11H102KD01D), C1 decap at CN7 input
14 | TM | O | 16 | TMP | O | 14 | STB4 | I | RA24 (MNR14E0ABJ223), CA2 (GNM314B11H102KD01D)
15 | TM | O | 17 | TMR2 | I? | 15 | Vlog | I
16 | STB3 | I | 18 | STB3 | I | 16 | TMP | O | C32 (GRM155B11H222KA01) to AGND, R28 (MCR01MZSF1002), C36 (GRM1552C1H470JZ01) decap to DGND at MCU, derived from Vcc and /HON
17 | STB2 | I | 19 | STB2 | I | 17 | TMR2 | I? | RA24 (MNR14E0ABJ223), CA1 (GNM314B11H102KD01D), JP18 (DNI) , Q7 (DTC124EUA), Q8 (DTA124EUA), Q9 (2SK2090-T1-A) circuit
18 | STB1 | I | 20 | STB1 | I | 18 | STB3 | I | RA23a (MNR14E0ABJ223), CA1 (GNM314B11H102KD01D)
19 | GND | - | 21 | GND | - | 19 | STB2 | I | RA23a (MNR14E0ABJ223), CA1 (GNM314B11H102KD01D)
20 | GND | - | 22 | GND | - | 20 | STB1 | I | RA23a (MNR14E0ABJ223), CA1 (GNM314B11H102KD01D)
21 | LATn | I | 23 | /LAT | I | 21 | GND | - | Connect to AGND
22 | DO | O | 24 | DI | O | 22 | GND | - | Connect to AGND
23 | VH | I | 25 | VH | I | 23 | /LAT | I | RA21 (MNR14E0ABJ223), CA3 (GNM314B11H102KD01D)
24 | VH | I | 26 | VH | I | 24 | DI | O | RA21 (MNR14E0ABJ223), CA3 (GNM314B11H102KD01D)
25 | SWn | I | 5 | Vlog | I | 25 | VH | I
26 | SW | O | 4 | HUP | O | 26 | VH | I | R32 (), CA2 ()
27 | MTAn | I | 27 | MTAn | I | 27 | MTAn | I | M14
28 | MTA | I | 28 | MTA | I | 28 | MTA | I | M14 (LB1936V-TLM-E), D4 (RB500V), D12 (RB500V), RA17 (MNR14E0ABJ223)
29 | MTBn | I | 29 | MTBn | I | 29 | MTBn | I | M15
30 | MTB | I | 30 | MTB | I | 30 | MTB | I | M15
1 | VSEN | I | 1 | Vcc2 | I | 1 | Vcc2 | I | ~1.46V (PWM @ 5V)
2 | PHE | O |  |  |  | 2 | CHOME | O | R63 (MCR01MZSF1502), C58 (GRM155B11H222KA01), C40 (GRM1552C1H470JZ01) decap to DGND at MCU
3 | PHK | - |  |  |  | 3 | CSEL | O | R64 (MCR10HJ181), C59 (GRM155B11H222KA01)
4 | MTA | I | 4 | MTA_2 | I | 4 | MTA_2 | I
5 | MTAn | I | 5 | MTAn_2 | I | 5 | MTAn_2 | I
6 | MTB | I | 6 | MTB_2 | I | 6 | MTB_2 | I
7 | MTBn | I | 7 | MTBn_2 | I | 7 | MTBn_2 | I
8 | NC | - |  |  |  | 8 | NC

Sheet: motor
AIN1 | AIN2 | BIN1 | BIN2 | AOUT1 | AOUT2 | BOUT1 | BOUT2 | STEP
1 | 1 | 1 | 0 | 0 | 0 | 1 | 0 | 4
1 | 0 | 1 | 0 | 1 | 0 | 1 | 0 | 5
1 | 0 | 1 | 1 | 1 | 0 | 0 | 0 | 6
1 | 0 | 0 | 1 | 1 | 0 | 0 | 1 | 7
1 | 1 | 0 | 1 | 0 | 0 | 0 | 1 | 0
0 | 1 | 0 | 1 | 0 | 1 | 0 | 1 | 1
0 | 1 | 1 | 1 | 0 | 1 | 0 | 0 | 2
0 | 1 | 1 | 0 | 0 | 1 | 1 | 0 | 3
 |  |  |  | MTA | MTAn | MTB | MTBn
1 | 0 | 1 | 0 | 1 | 0 | 1 | 0 | 2
1 | 0 | 0 | 1 | 1 | 0 | 0 | 1 | 3
0 | 1 | 0 | 1 | 0 | 1 | 0 | 1 | 0
0 | 1 | 1 | 0 | 0 | 1 | 1 | 0 | 1

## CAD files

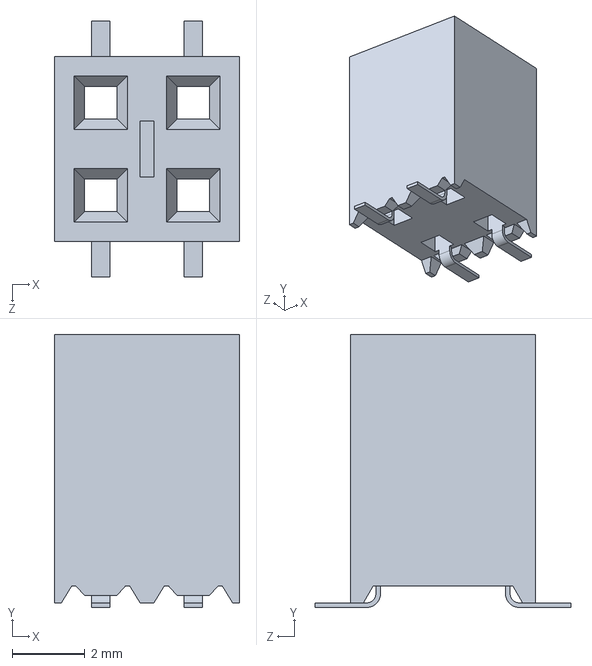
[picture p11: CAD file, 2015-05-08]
hw/docs/connectors/SSM-102-X-DV.step
5.08 x 7.49 x 7.04 mm

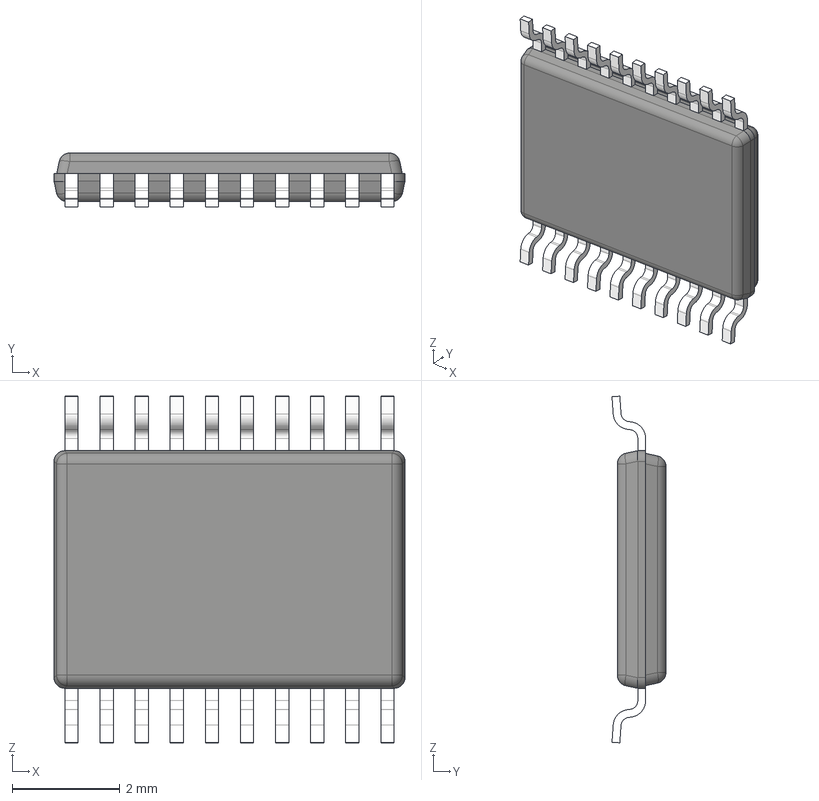
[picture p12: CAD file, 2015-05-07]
hw/docs/misc/SN74LVC244A/PW0020A.stp
6.50 x 1.00 x 6.42 mm
BODY_MTC20
LEAD_MTC20 x 20

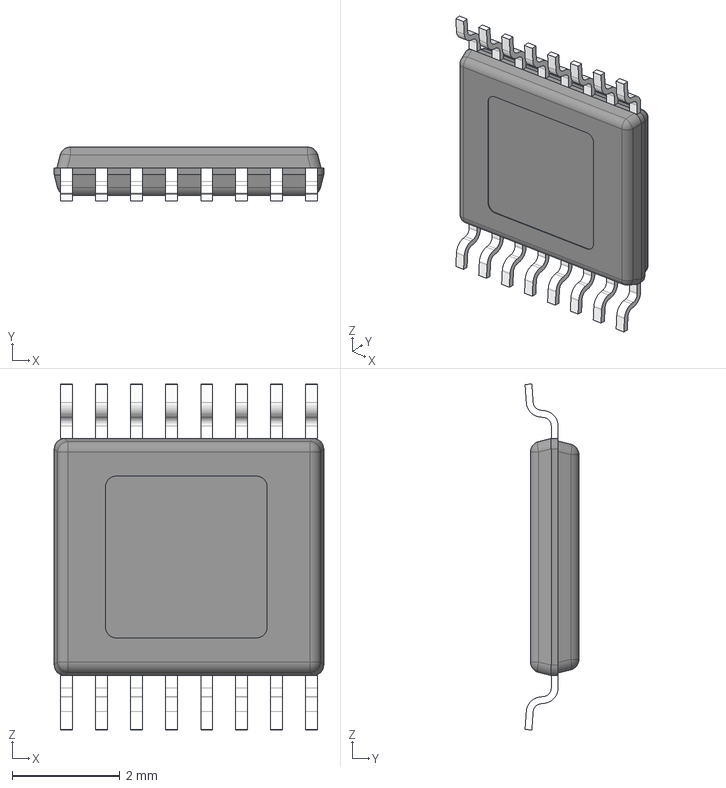
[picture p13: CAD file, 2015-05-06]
hw/docs/motor/DRV8833C_PWP_16/drv8833c.stp
5.00 x 1.00 x 6.42 mm
BODY_MXA16A
LEAD_MXA16A x 16

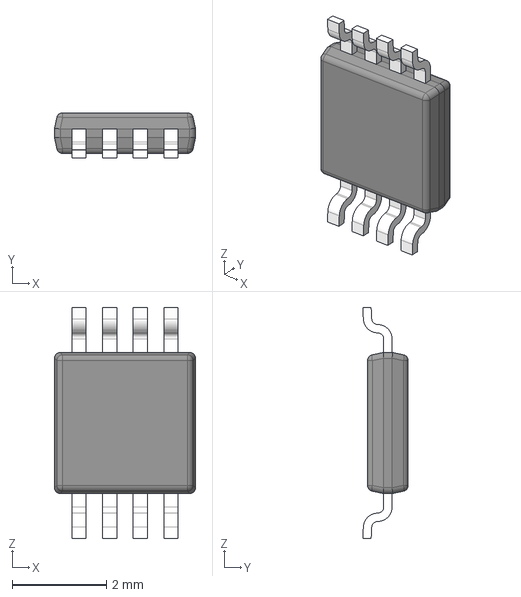
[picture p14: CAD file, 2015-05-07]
hw/docs/power/lm3478/LM3478_DGK_8_DGK0008A.stp
3.00 x 0.965 x 4.90 mm
BODY_MUA08A
LEAD_MUA08A x 8

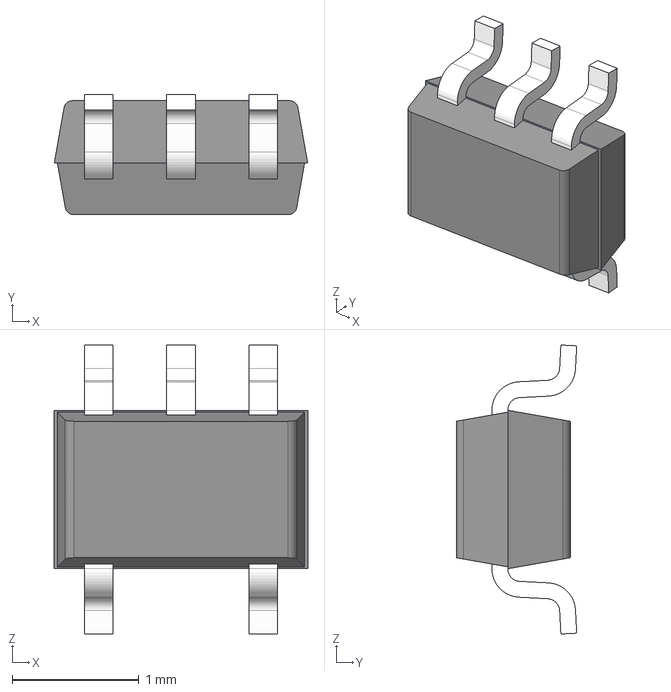
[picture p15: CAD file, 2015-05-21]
hw/docs/power/sn74lvc1g08/sn74lvc1g08_DCK0005A.stp
2.00 x 0.95 x 2.28 mm
BODY_MAA05
LEADS_MAA05A

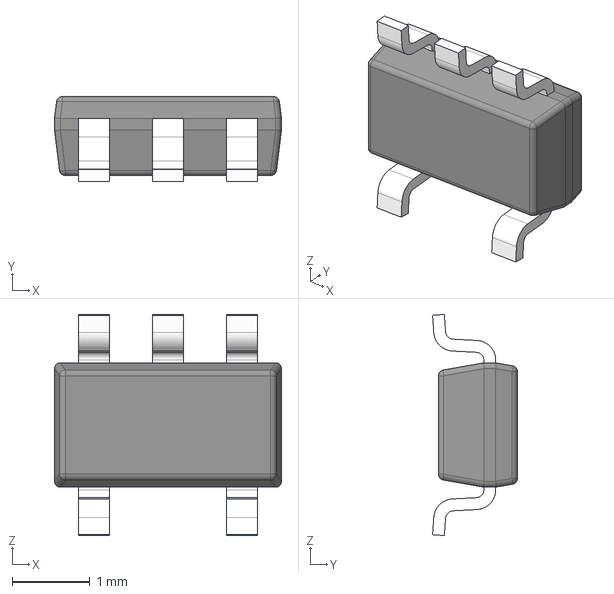
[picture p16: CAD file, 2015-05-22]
hw/docs/watchdog/TPS3126E12_DBV0005A.stp
2.92 x 1.09 x 2.84 mm
BODY_MF05A
LEAD_MF05F x 5

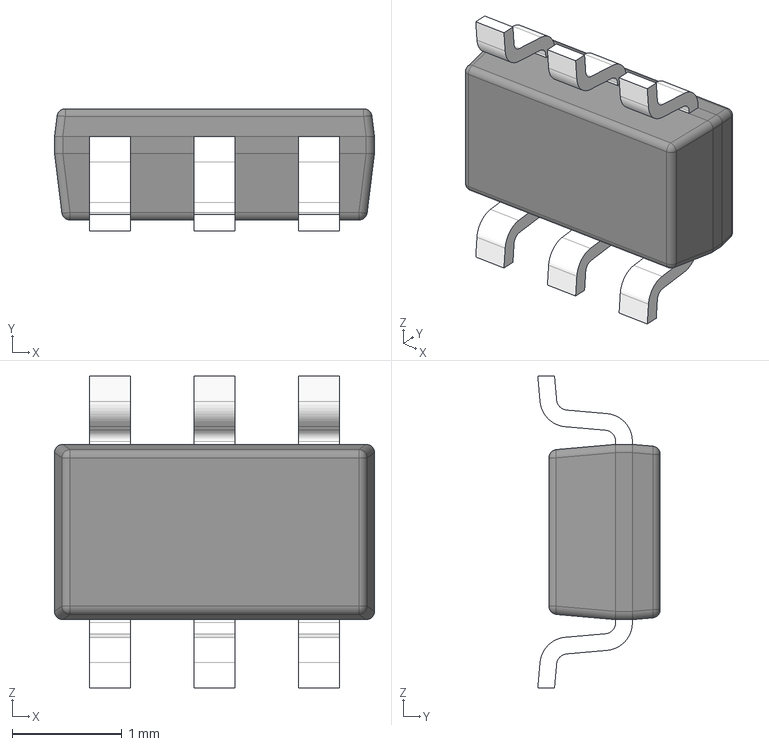
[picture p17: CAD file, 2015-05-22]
hw/docs/watchdog/TPS3813K33_DBV0006A.stp
2.92 x 1.12 x 2.84 mm
BODY_MF06A
LEAD_MF06A x 6

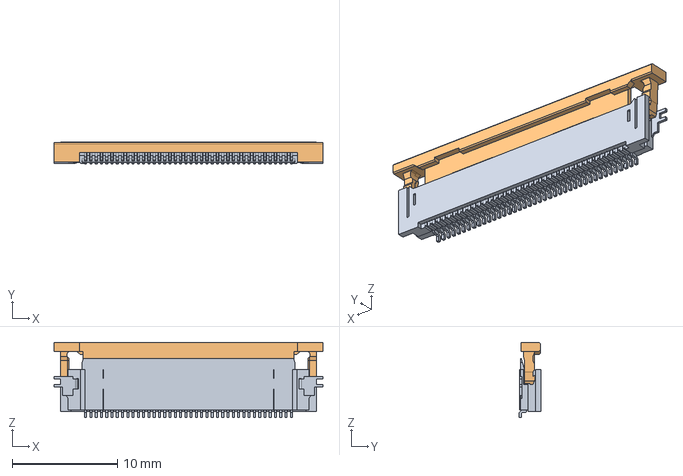
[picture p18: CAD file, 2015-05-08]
hw/docs/display/541324062.stp
25.5 x 2.05 x 7.15 mm

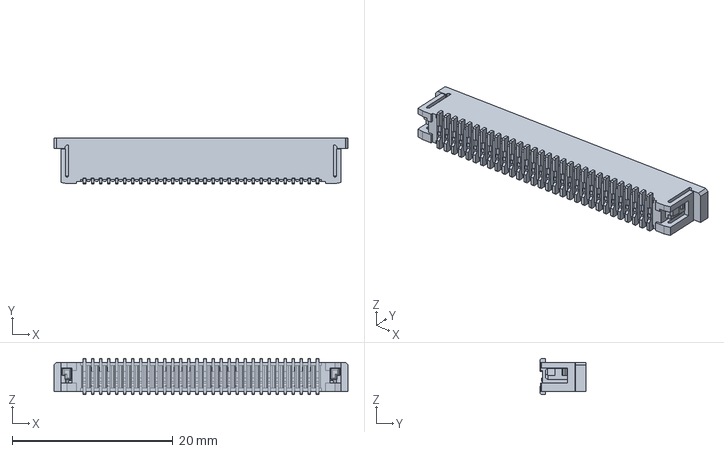
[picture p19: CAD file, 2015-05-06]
hw/docs/connectors/526103033.stp
36.6 x 5.75 x 4.50 mm

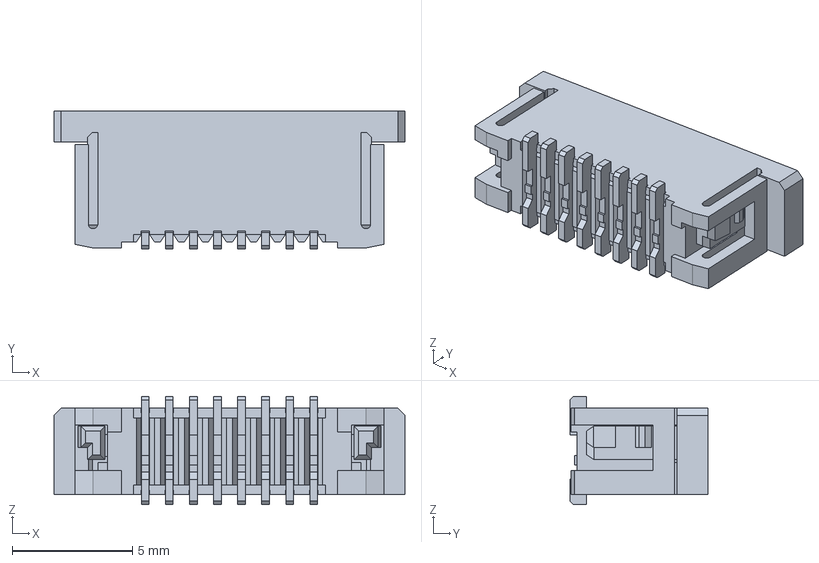
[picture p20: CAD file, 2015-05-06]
hw/docs/connectors/526100833.stp
14.6 x 5.75 x 4.50 mm

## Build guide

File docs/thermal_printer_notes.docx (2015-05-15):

Thermal Printer Notes

Thermal Printer Technical Manual

“Thermal Printer Techical Manaul 2_22_2008 (2).pdf”

- Fujitsu FTP-628USL401 print head made by Fujitsu Component Ltd.
  - Non-impact, line type which has heating elements lined up throughout the printing width
  - The mechanism is simple, compact, maintenance is easy, and use is stable even in a poor environment, high speed printing possible. Thermo-sensitive paper can be stored for a long time, life is guaranteed for 10 years
  - Thermal printers have a general business use (POS, printing labels/receipts, ticket machine)
  - Disadvantages: special paper required, storage of paper is dependent on the environment
- Connectors
  - Print head connector (CN3), 30-pin
    - Molex 52610-3071 -> 52610-3072
  - Cutter connector (CN4), 8-pin
    - Molex 52610-0871 -> 52610-0872
- Power
  - Print head 4.2-8.5VDC 0.38A (2.4A peak) at 7.2V
  - Motor 4.2-8.5VDC 1A max
  - Cutter 4.75-8.5VDC 1A max
  - Logic 3.0-5.25VDC 0.1A max
  - VDD_5V from BBB uses DC power supply rated at 3A (should be enough to cover max(printhead+BBB)
- Sensing
  - Thermistor; measures print head temperature
  - Photo-interruptor; detects marks and paper out, paper run, home position detection
  - Sliding switch; releases platen, platen open detection
- Motors
  - Paper feed motor
  - Cutter motor
  - Drive voltage is 4.2~8.5 V
  - Max printing speed is 80 mm/s
- Functionality (of interface board)
  - Test print function
  - Paper out detection (paper must be kept within 1mm from the photo sensor)
  - Paper near end detection (external mechanical switch)
  - Platen open detection
  - Thermal head temp abnormal detection (thermistor)
  - Blow out fuse detection
  - Head voltage abnormality detection
  - Cutter trouble detect
  - Motor power saving function
  - Mark detection (GS < command)
  - MCU operation abnormality detection (WDT?)
  - Power on/off sequence detection
  - Motor over-current protection (fuse)
  - Hardware timer
  - Dots/line
  - Dots font
  - Bar code commands
  - Character registration
  - Paper feed function (/ATF signal)
- Communication
  - Data to the main unit must be received at a required speed (>246 Kbps)
  - Image data by driver software
  - Centronics parallel interface can support 224 kbps
- Installation conditions
  - Installation condition 1-1 with paper feed direction upward is the most preferable so that paper moves debris to the outside
  - Or condition 2-1 with cutter; should prevent paper debris from dropping into itself causing double cutting
  - Roll paper should be loaded with direction outward away from the printer (condition 3-1)
- Printer Drive Circuit

Signal Name | Signal Content | Description | PRU Signal
DATA IN(DI) | Head input data | Data input signal to head
CLOCK (CLK) | Data transfer clock | Synchronization clock for transmitting head data
DATA OUT (DO) | Head output data | Data output of end of data. Some product do not have this signal (NC). | Serial resistor to prevent SC
/LATCH | Data latch signal | Pulse signal for latching data to head
STROBE (STB) | Strobe terminal | Power ON gate signal having both positive and negative logic
TH | Thermister | Output at both ends or only at one end
VDD/GND (VDD) | Head logic power supply | | VDD_3V3
VH/GND (VH) | Head power supply | | VDD

  - In the case of battery driving, all lines connected to the head, including the power supply, must be set to "Low" in order to decrease power consumption during standby.
  - The clock frequency depends on the IC in use, and 6 MHz or 8 MHz is used, or 16 MHz
  - CLK terminal needs noise removal like decoupling capacitor (normally 100 – 1000 pF)
  - DI and /LATCH signals needs capacitor as well (100 – 1000 pF)
  - The data (DI) is loaded at the rise of the clock (CLK), and the data must be held stably before and after the rise of the clock, and during periods of tsetup and thold.
  - Clock frequency = NWV / 15625 (MHz)
  - recommend not to increase frequency unnecessarily to avoid noise (increased frequency means increased margin of transfer)
  - The /LATCH pulse is very narrow, so if the capacity of the capacitor is too large, the pulse may not rise, and the latch may be missed (diagram on pg. 48)
  - Input the STROBE signal via the gate based on the hardware timer (see Fig. 46)
  - We recommend that 1 strobe is comprised of a plurality of retrigger pulses to prevent noise affecting the output
  - A large amount of current flows through VH-GND, therefore the VH-GND pattern must take sufficient distance from other signal lines so that voltage is not dropped by the current
    - Connect a 100uF or higher capacitor
    - As a rule, however, connect the GNDs (for VDD and VH) together at the bottom of the power supply input connector terminal inside the substrate.
  - Be certain to wire the logic power supply VDD-GND (VDD) sufficiently away from heavy current patterns, so that noise does not enter from the outside.
    - Also add a 47uF or higher to the logic supply (VDD)
  - If a thermal head is used, the voltage being applied to the head (VH) must be cut during standby. For the switching element, a relay and MOS-FET transistors, which do not cause much leak current, must be used. (see Fig. 50 on pg. 52)
    - For selection, confirm the maximum energizing load current and minimize the drop in voltage.
  - Power on
    - In the initial processing immediately after power ON, be certain to transfer NULL data "0" to the head, and perform latch processing.
    - As a rule, design a sequence such that VH becomes within VDD + 1V at the maximum when VDD rises or falls 80% of the logic applied voltage or more.
    - It is desirable that the rise time of the power supply is short, and design such that the logic voltage rises from 40% to 80% of applied voltage within 10 msec. (see Fig. 52)
    - Latch up
      - To prevent this, it must be noted that reverse voltage is not generated between VDD and the input terminal.
    - VDD/VH is also turned OFF during a hardware reset period.
    - Design circuits such that all control signals are also forcibly set to "Low" during a reset period.
    - Set hardware so that the head is OFF, the motor is OFF and the interface is busy during the reset period.
  - Precautions for grounding
    - During printing, a very heavy current flows through GND (VH) depending on the number of energized dots. Therefore if this current flows into GND (VDD), the logic potential may change and a malfunction may occur.
    - Install the power supply connector near the head, and connect the GND (VH) and the other GND patterns at the bottom of the connector.
  - Precautions for VH
    - Ensure power supplies support such high-speed peak current
    - Power supply which can support peak load current is necessary
    - Voltage may instantaneously drop and cause printing blurs if the peak response is low.
    - Peak load countermeasure in Fig. 57
    - one method is to install an LC filter in the power supply input terminal section, but an allowable DC load of the coil must be checked
  - Thermister control
    - The resistance value of the thermister changes depending on the temperature. Temperature is detected by detecting the change of the resistance value.
    - Normally a thermister is input to the AD converter terminal of the CPU
    - Thermister processing in Fig. 58
      - Generate a highly accurate reference voltage using a shunt regulator, for example, and detect the resistance value by dividing this reference voltage.
      - For an external resistor, use a product with a precision temperature compensation that is less than 2%.
      - For the output stage, it is recommended to attach an appropriate temperature compensation capacitor based on the confirmation of ESD
      - Table 6 on pg. 58
  - Motor drive
    - A stepping motor is used for driving the paper feed motor and the cutter motor of the FTP-607/608/609MCL400 series.

Motor type | Signal name | Remarks
Stepping motor | MT-A | Bipolar Phase A
| MT-/A | Bipolar phase /A
| MT-B | Bipolar phase B
| MT-/B | Bipolar phase /B
DC motor | MT+ | Motor terminal (+)
| MT- | Motor terminal (-)

    - The FTP-608 series uses bipolar systems for the stepping motor drive system
    - Maximum frequency is 3000 at 8.0V ~ 8.5V
    - Controlling phase: the 1-2-phase excitation drive system has smaller step sizes and less noise

Step | MT-A | MT-B | MT-/A | MT-/B | Step | MT-A | MT-B | MT-/A | MT-/B
0 | 0 | 0 | 0 | 1 | 0 | 0 | 0 | 1 | 1
1 | 0 | 0 | 1 | 1 | 1 | 0 | 1 | 1 | 0
2 | 0 | 0 | 1 | 0 | 2 | 1 | 1 | 0 | 0
3 | 0 | 1 | 1 | 0 | 3 | 1 | 0 | 0 | 1
4 | 0 | 1 | 0 | 0
5 | 1 | 1 | 0 | 0
6 | 1 | 0 | 0 | 0
7 | 1 | 0 | 0 | 1

  - Motor drive circuit
    - When a stepping motor is driven, be certain to perform constant current control if a condition under which excitation current for phase exceeds 500 mA occurs
    - For example, in the case of the FTP-608 MCL series, a 10 motor is used… Therefore a constant current control is required if the applied voltage for driving the motor is 5.6V or more.
    - If speed becomes slower, however, the motor current rises continually, and reaches the maximum current. (Fig. 60)
    - Maximum excitation current of the motor is 450mA with motor diameter at 15mm
    - Use one of the many ICs available that have a constant current circuit for 24V motor driving ICs (see example circuit in Fig. 62 which uses a A6919SLB)
    - Drive ICs for low voltage rarely have these functions. Therefore a feedback circuit must be created to create a constant current circuit. (see Fig. 64)
    - the A-/A phase feedback circuit and the B-/B phase feedback circuit must be separated. The ground side must be separated inside the motor IC.
    - Some MPUs have a built-in PWM function, and external circuits can be decreased by using this function. This is a way of limiting the motor current to be constant by switching each phase output signal.
      - Use PWM for the pulse, and do not perform switching until current reaches a predetermined current.
      - be certain to attach a fuse as a safety measure to the motor circuit to prevent smoking and combustion by a motor short circuit
    - As a safety measure, be certain to insert a fuse in the power supply line to prevent smoking and combustion.
    - For acceleration/deceleration control, normally a trapezoidal control method is used. For example, it is assumed that speed is increased from 800 PPB to a maximum of 3000 PPS.
    - In the FTP-608 MCL series, maximum frequency is about 3000 PPS (8.0V or more)
    - In the FTP-608 MCL series, the drive voltage may fluctuate in a 4.2 8.5V range.
    - Ton define in section 7.3
  - Thermal Shutdown
    - If the timing difference between two ICs is major, a short circuit current may be generated, so mount the ICs close together with a short interconnect, and minimize the difference of signals between ICs.
  - Motor for cutter
    - A cutter requires a home position. A home position sensor is controlled by a photo sensor
  - Sensors
    - No paper detection (photo interrupter, Fig. 71)
    - Platen up detection (micro switch, Fig. 70)
    - Cutter home position detection (photo sensor, Fig. 71)
    - Temperature detection (thermister, Fig. 58)
  - Photo interrupter for paper detection

Signal name | Function | Description
PHK | Photo diode cathode | Sets IF by resistance r
PES | Photo transistor emitter | Generates voltage of IC x R by resistance R
VSNS | Photo interrupter power supply | Switching by power supply recommended

    - Switch the power supply to the photo sensor, and turn it OFF during standby.
    - Reading output V (PES) from the photo interrupter by an AD converter is recommended.
    - Connect pull down resistors on PHK and PES based on Fig. 71
    - Recommend making the threshold programmable for VSNS
    - Normally, the IF is ~20mA

FTP-628CU451 Product Specification

“628CU451 PRELIMINARY Ver01(050531).pdf”

Datasheet

“ftp-628mcl401.pdf”

- Low profile (height 21.8mm, width 81.2mm, depth 42.2mm), weighs 98g
- High speed printing at a maximum of 80 mm/s (640 dotlines/s) at 8.5V, 60mm/s for EVM
- Interface board for cutter support (FTP-628DSL491R parallel (centronics) / serial (rs-232c) )
- Dot structure: 384 dots/line
- Dot pitch (horizontal) dot density: 0.125mm (8 dots/mm)
- Dot pitch (vertical) line feed pitch: 0.125mm (8 dots/mm)
- Effective printing area: 48mm
- Number of columns: ANK 32 columns/line (maximum 12 x 24 dot font)
- Paper width: 58mm
- Paper diameter: 60mm (EVM)
- Paper thickness: 60 to 85 um
- Power supply:

For print head | 4.2 - 8.5 VDC average current, 1.8 (2.4)A at 7.2V (print ratio: 12.5%, print speed: 60mm/sec. )
For motor | 4.2 - 8.5 VDC, 1A maximum
For cutter motor | 4.75 - 8.5 VDC, 1A maximum
For logic | 3.0 to 5.25 VDC, 0.1A maximum

PRU/Printer Communication

- AM335x PRU base address = 0x4A300000
- Serial or parallel interface (RS-232C or Centronics)
- Buffer for storing data in memory?
- Resolution: 8dots/mm
- For image mode, the max # dots/line: 384 (there are 384 heating units)
- Max printing speed is 80mm/s at 8.5V, 25C
- Max power consumption is 2.9A (4.8A spike) for low speed print mode
- VDD for logic is 5V +/- 5%, max current is 0.3A

Status LEDs? (5V power supply, error detection light)

Paper Feed Motor

- Countermeasures
- Fuse
- Voltage: 4.75 ~ 8.5V
- Max current: 1.1A
- Max current simultaneous motor: 1.5A
- M15SP-1N motor has 18 degrees/step → 20 steps/revolution (2 phase excitation)
- *Caution：Since there is fear of breakage of a head, be sure to use head voltage less than 8.5V .
- The head driving power supply is switched by FET, which is controlled by MCU.
- Motor excitation is shutdown by a hardware timer to prevent motor smoking caused by an operation abnormality. Limit the applied pulse width of the head by a hardware timer to prevent head burning by fixing the logic of the thermal head enable signal.
- Motor drive circuit description on pg. 59
- Limit current to 500mA

Cutter Motor

- Countermeasures
- Fuse
- Cutter Home Position
  - Photo interrupter sensor
  - When the cutter blade is not in the home position at initialization, the printer automatically positions the cutter.
  - When a paper cut command is received in the state of cutter un-connecting, it will be in a Hardware abnormality state

Initialization and Reset

- Power on requirements
- Timing requirements
- When watchdog is occurred, printer goes internal reset state and MCU operation is stopped.
- This function prevents burning of the head caused by the reverse order disconnection of the logic power supply and power supply for the head.
- Standby (all signals and power supply set to low during standby; Be certain that wrap around from the circuit side logic power supply is not generated)

Head Temperature

- Thermistor circuit description on pg. 56
- Hardware timer for protection
- FET
- Temperature is detected by the thermistor inside the thermal head to protect the head from heating.
- When abnormal temperature (about 70℃) is detected, the printer stands by in busy status until the temperature drops to the specified temperature (about 60℃).

Paper Detection

- Photo interrupter for paper detection, mark detection
- During printing or feeding paper, a paper run out is detected when the sensor continuously detects a black level for about 7mm.
- When the printer detects a paper run out during printing, and if currently printing data exists, the printer automatically enters off-line (BUSY) status after printing one line.
- When paper run out is detected, driving of the motor is turned OFF. (take care in software)
- VSNS - photo interrupter power supply
  - Switch the power supply to the photo sensor, and turn it OFF during standby.
- PHK – photo diode cathode sets current IF by resistance r
  - Normally the IF is set to IF = about 20 mA.
- PES – photo transistor emitter generates voltage of IC x R
  - Reading output V (PES) from the photo interrupter by an AD converter is recommended.
  - We therefore recommend making the threshold programmable.

Platen Switch

- Microswitch for platen open detection
- When the printer detects platen open during printing, the printer stops driving the head and the motor in one line unit, and the printer automatically enters off-line (BUSY) status.

Andreas’ Cape Design

P8.1 →GND

P8.2 →GND

P8.20 → R31-13 (/NFAULT)

P8.21 → R30-12 (sn74lvc244a enable)

P8.27 →R30-8 (AIN1)

P8.28 →R30-10 (RIN1)

P8.29 →R30-9 (AIN2)

P8.30 →R30-11 (RIN2)

P8.39 →R30-6 (/LATCH)

P8.40 →R30-7 (DATA_IN)

P8.41 →R30-4 (/STB5-6)

P8.42 →R30-5 (CLK)

P8.43 →R30-2 (/STB2-3)

P8.44 →R30-3 (/STB4)

P8.45 →R30-0 (PSENSE)

P8.46 →R30-1 (/STB1)

P9.1 →GND

P9.2 →GND

P9.3 →3.3V VCC

P9.4 →3.3V VCC

P9.5 →5V VCC

P9.6 →5V VCC

P9.7 →SYS 5V VCC

P9.8 →SYS 5V VCC

P9.9 →PWR_BUT

P9.10 →SYS_RESETn

P9.26 →R31-16 (POUT)

P9.43 →GND

P9.44 →GND

P9.45 →GND

P9.46 →GND

3 versions of the cape:

- TPcape Basic (basic features, headers for extended output, VDD_5V)
- TPcape (with ADC, higher voltage)
- TPcape Ultra (with LCD)
- TPcape Basic
  - No photo interruptor
  - No thermistor
  - No platen detection
  - Just stepper signals, print head signals, strobes

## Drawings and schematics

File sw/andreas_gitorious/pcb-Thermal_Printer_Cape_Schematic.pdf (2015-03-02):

A

A

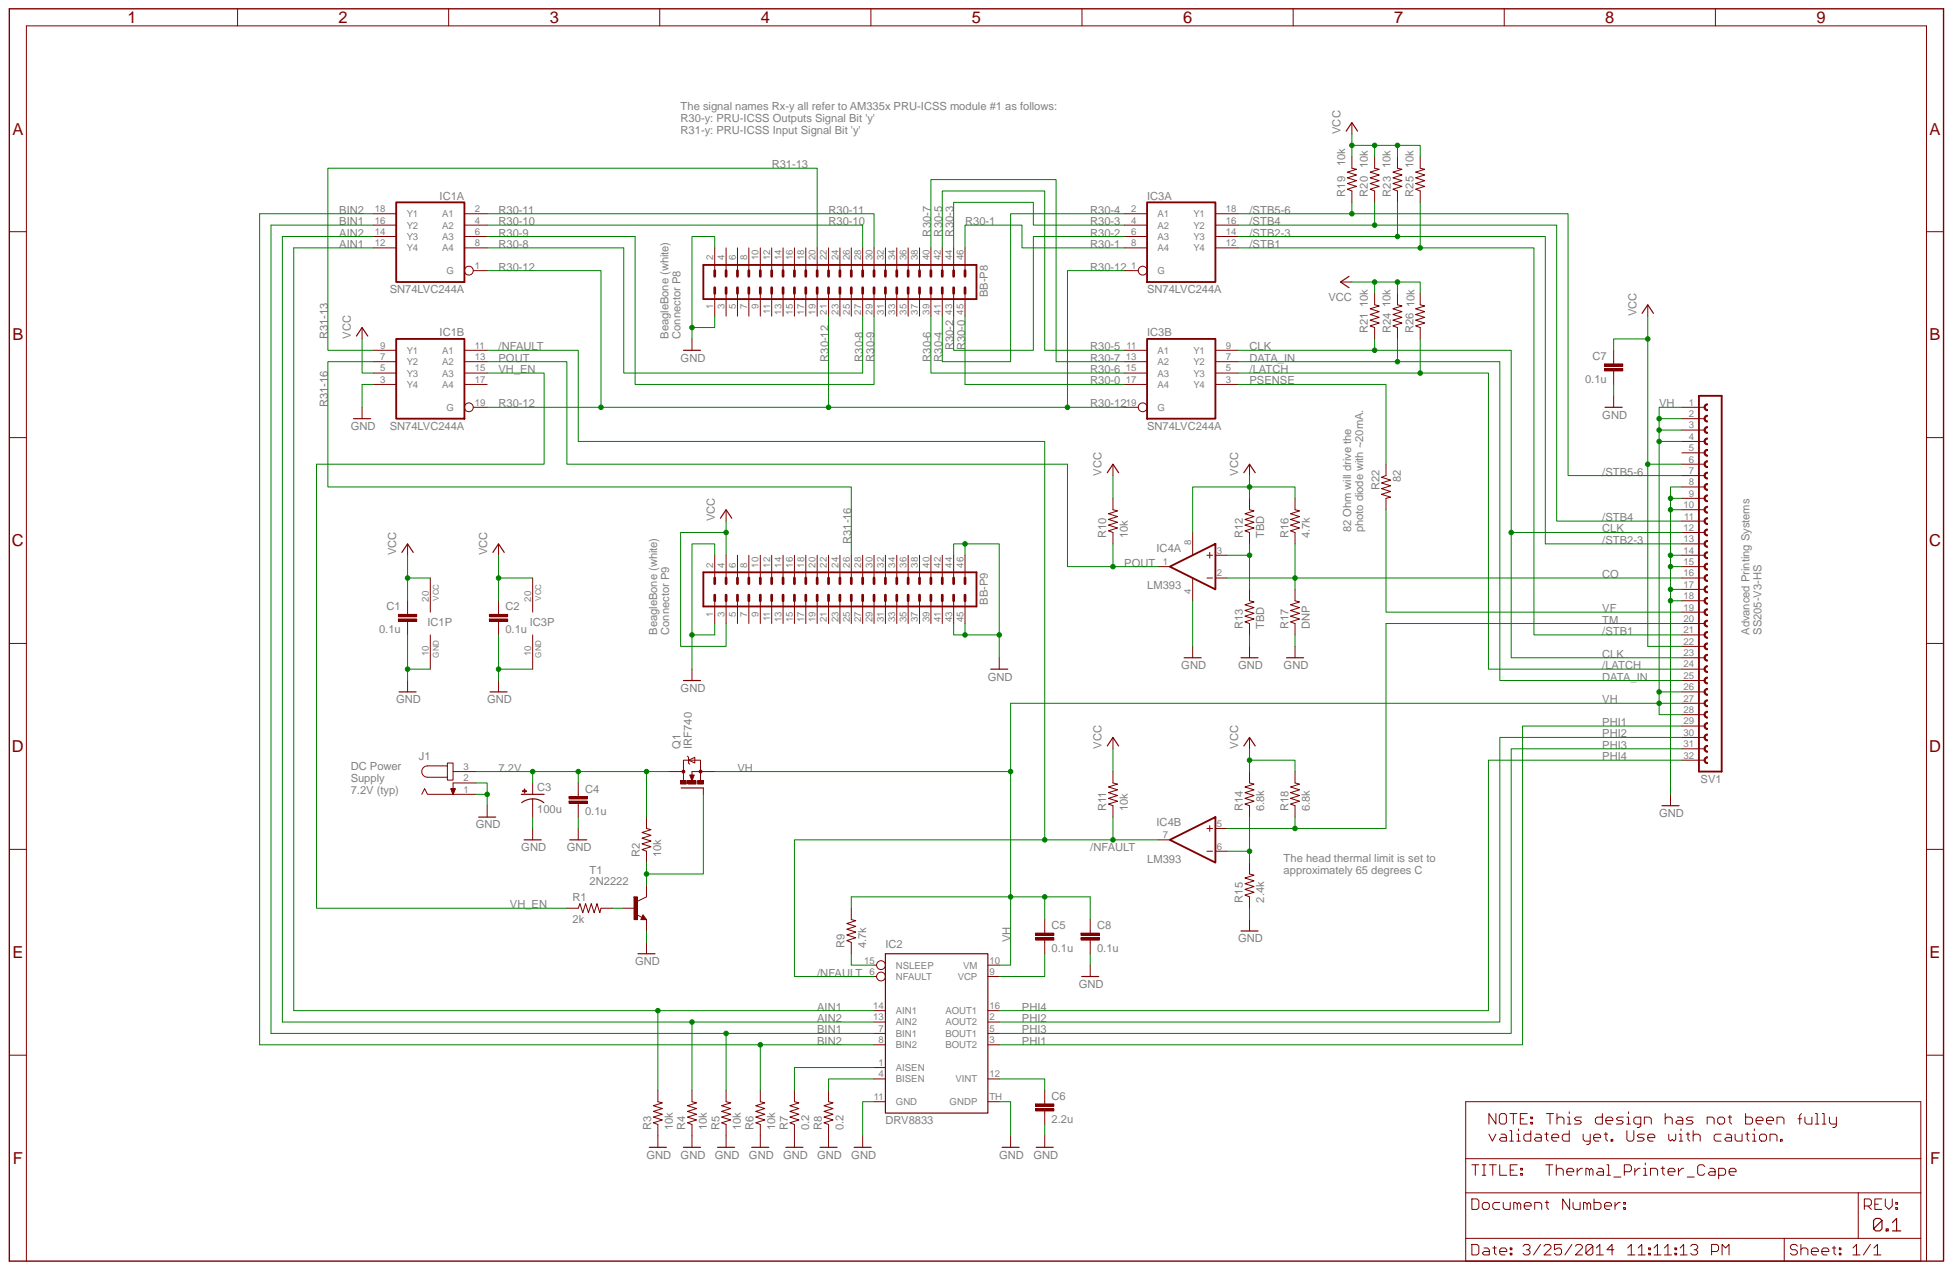
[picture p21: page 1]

The signal names Rx-y all refer to AM335x PRU-ICSS module #1 as follows:
R30-y: PRU-ICSS Outputs Signal Bit 'y'
R31-y: PRU-ICSS Input Signal Bit 'y'

82 Ohm will drive the

The head thermal limit is set to
approximately 65 degrees C

GND GND

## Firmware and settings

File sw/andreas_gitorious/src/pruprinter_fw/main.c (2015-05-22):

/*
 * main.c
 *
 * AM335x PRU-based Thermal Printer Driver Low-Level Firmware
 *
 * Program waits in a processing loop for a host interrupt to arrive. After
 * it received one it starts processing the print job located in the printer
 * queue in the PRU shared memory. After it's done processing the job it then
 * issues an interrupt back to the host. At this time the host can also read
 * out the status bits located in the printer queue status register.
 *
 * Written by Andreas Dannenberg, 01/01/2014
 *
 * Copyright (C) 2014 Texas Instruments Incorporated - http://www.ti.com/
 * ALL RIGHTS RESERVED
 */

// TODO: Add functionality to monitor the printer activity duty cycle

#include <stdint.h>
#include <stdbool.h>
#include "pru.h"
#include "pruprinter.h"

// Activate below definition to let the printer make use of the temperature
// sensor that's integrated into the motor-driver H bridge. If activated the
// temperature will be monitored throughout the print job and the job will
// get cancelled if the temperature exceeds safe limits and an error will get
// reported back to the host.
#define PRINTER_USE_THERMAL_SENSOR

// Activate below definition to let the printer make use of the end-of-paper
// sensor integrated into the printer assembly. If activated and the paper runs
// out during printing the job will get cancelled and an error will get reported
// back to the host.
#define PRINTER_USE_PAPER_SENSOR

// Interface to the printer circuitry. The bits defined here map to bits in
// PRU 1 core register R30 for outputs and to bits in R31 for inputs.
#define PRINTER_OUT_PAPER_SENSE     (1 << 0)    // BB P8.45 - Powers the paper-sense circuit
#define PRINTER_OUT_STB1_N          (1 << 1)    // BB P8.46 - Strobe dots 321 to 384
#define PRINTER_OUT_STB23_N         (1 << 2)    // BB P8.43 - Strobe dots 193 to 320
#define PRINTER_OUT_STB4_N          (1 << 3)    // BB P8.44 - Strobe dots 129 to 192
#define PRINTER_OUT_STB56_N         (1 << 4)    // BB P8.41 - Strobe dots 1 to 128
#define PRINTER_OUT_CLK             (1 << 5)    // BB P8.42 - Serial clock
#define PRINTER_OUT_LAT_N           (1 << 6)    // BB P8.39 - Latch signal
#define PRINTER_OUT_MOSI            (1 << 7)    // BB P8.40 - Serial data
#define PRINTER_OUT_A1              (1 << 8)    // BB P8.27 - Motor driver A1
#define PRINTER_OUT_A2              (1 << 9)    // BB P8.29 - Motor driver A2
#define PRINTER_OUT_B1              (1 << 10)   // BB P8.28 - Motor driver B1
#define PRINTER_OUT_B2              (1 << 11)   // BB P8.30 - Motor driver B2
#define PRINTER_OUT_PWR_N           (1 << 12)   // BB P8.21 - Powers the printer head
#define PRINTER_IN_ALARM_N          (1 << 13)   // BB P8.20 - Thermal alarm
#define PRINTER_IN_PAPER_OUT        (1 << 16)   // BB P9.26 - Paper out

// Convenience macros for accessing the input/output bits in the core registers
#define PRU_OUT_SET(x)              { __R30 |= (x); }
#define PRU_OUT_CLR(x)              { __R30 &= ~(x); }
#define PRU_IN(x)                   (__R31 & (x))

// Bit-indexes of the printer line when certain strobe signals need to be
// asserted
#define STB1_BYTE_INDEX             (384 / 8 - 1)
#define STB23_BYTE_INDEX            (320 / 8 - 1)
#define STB4_BYTE_INDEX             (192 / 8 - 1)
#define STB56_BYTE_INDEX            (128 / 8 - 1)

// General PRU-timing related definitions. Note that for the delay definitions
// to work the PRU core frequency must have been defined correctly.
#define F_PRU_OCP_CLK_HZ            ((uint32_t)200E06)
#define DELAY_5_MS                  ((uint32_t)(F_PRU_OCP_CLK_HZ * 0.005))
#define DELAY_100_MS                ((uint32_t)(F_PRU_OCP_CLK_HZ * 0.100))
#define DELAY_500_MS                ((uint32_t)(F_PRU_OCP_CLK_HZ * 0.500))

// Printer communication-related timing definitions. Those come straight from
// the printer head's datasheet.
#define DELAY_TW_CLK                ((uint32_t)(F_PRU_OCP_CLK_HZ / 8E06 / 2))
#define DELAY_TSETUP_DI             ((uint32_t)(F_PRU_OCP_CLK_HZ * 70E-09))
#define DELAY_THOLD_DI              ((uint32_t)(F_PRU_OCP_CLK_HZ * 30E-09))
#define DELAY_TSETUP_LAT            ((uint32_t)(F_PRU_OCP_CLK_HZ * 300E-09))
#define DELAY_TW_LAT                ((uint32_t)(F_PRU_OCP_CLK_HZ * 200E-09))
#define DELAY_THOLD_LAT             ((uint32_t)(F_PRU_OCP_CLK_HZ * 50E-09))
#define DELAY_TSETUP_STB            ((uint32_t)(F_PRU_OCP_CLK_HZ * 300E-09))
#define DELAY_TD0                   ((uint32_t)(F_PRU_OCP_CLK_HZ * 3000E-09))
#define DELAY_TD1                   ((uint32_t)(F_PRU_OCP_CLK_HZ * 3000E-09))

// The below delay determines how long the printer dots will be energized. The
// exact value needed depends on various conditions. See printer head datasheet
// for more information.
#define DELAY_STB                   ((uint32_t)(F_PRU_OCP_CLK_HZ * 1E-03))

// The below delay determines the paper feed speed. The printer driver waits at
// least the specified time between stepper motor half-steps. The below value
// corresponds to a paper feed speed of 60mm/s. See printer head datasheet for
// more information.
#define DELAY_HALF_STEP             ((uint32_t)(F_PRU_OCP_CLK_HZ * 1.041667E-03))

// General helper macro - determine and return the maximum of two given values
#define MAX(a, b)                   (((a) > (b)) ? (a) : (b))

// Map the PRU shared RAM that is used as the printer queue to a local variable
// for easier access.
volatile far PRINTER_Queue queue __attribute__((cregister("C28_SHARED_RAM", far), peripheral));

// Keeps track of the current state of the stepper motor
static uint8_t motorStepIndex;

// Init and test functions
static void initPRU(void);
static void initIEP(void);
static void setIepCompareEvent0(const uint32_t count);
static void waitForIepCompareEvent0(void);
static void initPrinterStatusRegister(void);
static void initPrinterOutputSignals(void);
static void testPrinterOutputSignals(void);

// Functions used for printing
static void processPrintJob(const PRINTER_JobItem *job);
static void printLine(const uint8_t dotData[]);
static void printerStrobe(const uint32_t strobeSignal);

// Functions for controlling the stepper motor
static bool initMotor(void);
static bool advanceMotorHalfStep(void);
static bool checkThermalAlarm(void);

// Paper management
static bool checkPaperSensor(void);

// Program entry point and event processing loop
int main(void) {
    // Perform various PRU and printer-related initialization
    initPRU();
    initIEP();
    initPrinterStatusRegister();
    initPrinterOutputSignals();

    // Process print jobs which get started through ARM-to-PRU interrupts until
    // during processing a command to shutdown the PRU is encountered. This will
    // allow us to concatenate several print jobs if needed without disrupting
    // the state of the print process.
    while (!queue.status.bits.pruHaltRequested) {
        // Wait until receipt of interrupt from host via PRU interrupt 1 from
        // local INTC. The INTC config maps this event to channel 1 (host 1).
        // For this to work the interrupt must have been enabled by the host
        // driver as well (via ESR0 or ESR1 registers).
        while ((__R31 & 0x80000000) == 0) {
        }

        // Clear status of system interrupt 22 event (ARM_PRU1_INTERRUPT) in
        // SECR1. This will reset the associated PRU interrupt 1 flag in __R31
        // that has been associated with channel 1 (host 1).
        CT_INTC.secr0 = 1 << 22;

        // Process the print job that was submitted by the host. In case we ever
        // need double-buffering we can easily split the available PRU memory
        // into two sections and alternate between them - filling one while
        // printing the other. processPrintJob() already supports such a scheme
        // through the use of a the pointer to the first print job item.
        processPrintJob((PRINTER_JobItem *)queue.jobItems);

        // Interrupt Host for print job completion. At this point (and only
        // then!) the host can/should also read out the printer driver's
        // status register.
        __R31 = PRU1_ARM_INTERRUPT;
    }

    // Before proceeding to power down the PRU let's wait for a little bit to
    // give the host a chance to see the PRU->ARM interrupt we triggered as we
    // will be disabling all the interrupts in the next step.
    __delay_cycles(DELAY_500_MS);

    // Halt PRU core. Before that, clear all system interrupts as required to
    // allow the PRU to power down. Note that because of the call to __halt()
    // the main() function will actually never return.
    CT_INTC.secr0 = 0xffffffff;
    CT_INTC.secr1 = 0xffffffff;
    __halt();
}

static void initPRU(void) {
    // Clear SYSCFG[STANDBY_INIT] to enable OCP master port
    CT_CFG.syscfg &= ~(1 << 4);

    // Set C28_POINTER base address to 0x0001_0000 which is the beginning of the
    // PRU shared memory region. This is were our printer queue will reside.
    CTPPR0 = 0x00000100;
}

// Many of the register initializations below are redundant when coming from a
// PRU reset as those bits get initialized by hardware. Nevertheless as a good
// practice to minimize dependencies let's re-initialize them with exactly the
// configuration we need.
static void initIEP(void) {
    // Select ocp_clk as the clock source for the IEP peripheral to ensure it
    // is synchronous with the PRU core clock. This is for cycle-accuracy and
    // also to make sure that there are no race conditions as we use the PRU
    // core to access the counroott register.
    CT_CFG.iepclk |= (1 << 0);

    // Ensure counter is disabled. Set default an increment value of 1.
    CT_IEP.global_cfg = (1 << 4);

    // Disable all compare registers and counter reset on compare 0
    CT_IEP.cmp_cfg = 0;

    // Reset Count register by writing '1' to each bit
    CT_IEP.count = 0xffffffff;

    // Disable compensation
    CT_IEP.compen = 0;

    // Clear overflow status bit by writing '1' to it
    CT_IEP.global_status = (1 << 0);

    // Clear match status bit for compare blocks 0 to 7 by writing '1' to each bit
    CT_IEP.cmp_status = 0xff;

    // Enable the counter
    CT_IEP.global_cfg |= (1 << 0);
}

static void setIepCompareEvent0(const uint32_t count) {
    // Enable IEP compare register 0
    CT_IEP.cmp_cfg |= (0x01 << 1);

    // Set compare value for compare block 0. We simply add the desired value
    // value to the current counter, effectively operating the timer in
    // continuous mode which allows us to operate and use all timer blocks
    // independently should this ever be needed.
    CT_IEP.cmp0 = CT_IEP.count + count;

    // Clear match status bit for compare block 0 by writing '1' to ensure that
    // we are really waiting for the event that is going to occur.
    CT_IEP.cmp_status = 0x01;
}

static void waitForIepCompareEvent0(void) {
    // Wait for compare match to occur. It's possible that the event has
    // already occurred while we were off doing other things. In this case we
    // will return right away.
    while (!(CT_IEP.cmp_status & 0x01)) {
    }

    // Disable IEP compare register 0
    CT_IEP.cmp_cfg &= ~(0x01 << 1);
}

static void initPrinterStatusRegister(void) {
    queue.status.all = 0;
}

// Initializes all thermal printer signals to put the printer into a safe and
// unpowered mode (which should ideally have happened already through U-Boot
// or the Kernel configuration). Note that the signals with inverse logic '_N'
// are set to high.
static void initPrinterOutputSignals(void) {
    PRU_OUT_CLR(PRINTER_OUT_A1);
    PRU_OUT_CLR(PRINTER_OUT_A2);
    PRU_OUT_CLR(PRINTER_OUT_B1);
    PRU_OUT_CLR(PRINTER_OUT_B2);
    PRU_OUT_SET(PRINTER_OUT_STB1_N);
    PRU_OUT_SET(PRINTER_OUT_STB23_N);
    PRU_OUT_SET(PRINTER_OUT_STB4_N);
    PRU_OUT_SET(PRINTER_OUT_STB56_N);
    PRU_OUT_CLR(PRINTER_OUT_CLK);
    PRU_OUT_SET(PRINTER_OUT_LAT_N);
    PRU_OUT_CLR(PRINTER_OUT_MOSI);
    PRU_OUT_CLR(PRINTER_OUT_PAPER_SENSE);
    PRU_OUT_SET(PRINTER_OUT_PWR_N);
}

// Function that cycles all low-level output signals in a specific sequence.
// Note that this function is only to be used during firmware/hardware
// development/debugging. It should NOT be used if the actual printer head is
// connected, otherwise damage may occur.
static void testPrinterOutputSignals(void) {
    const uint32_t testVector[] = {
        PRINTER_OUT_A1,
        PRINTER_OUT_A2,
        PRINTER_OUT_B1,
        PRINTER_OUT_B2,
        PRINTER_OUT_STB1_N,
        PRINTER_OUT_STB23_N,
        PRINTER_OUT_STB4_N,
        PRINTER_OUT_STB56_N,
        PRINTER_OUT_CLK,
        PRINTER_OUT_LAT_N,
        PRINTER_OUT_MOSI,
        PRINTER_OUT_PAPER_SENSE,
        PRINTER_OUT_PWR_N
    };

    uint16_t i;

    while (1) {
        // Iterate through the entire test vector. Turn each output on for 0.5s
        // before turning it off again and waiting another 0.5s.
        for (i = 0; i < sizeof(testVector) / sizeof(testVector[0]); i++) {
            PRU_OUT_SET(testVector[i]);
            __delay_cycles(DELAY_500_MS);
            PRU_OUT_CLR(testVector[i]);
            __delay_cycles(DELAY_500_MS);
        }
    }
}

static void processPrintJob(const PRINTER_JobItem *job) {
    PRINTER_JobItem *currentItem = (PRINTER_JobItem *)job;
    bool endJob = false;

    while (!endJob) {
        switch (currentItem->command) {
        case PRINTER_CMD_OPEN:
            // (Re-)Initialize all printer output signals to a known-safe state.
            initPrinterOutputSignals();
            __delay_cycles(DELAY_5_MS);
            // Turn on the printer head control logic and the end-of-paper
            // sensor supply. Then, wait a predetermined amount of time for the
            // voltages to settle. This amount can likely be made much shorter
            // however let's be conservative for now until the final demo
            // hardware been designed.
            PRU_OUT_CLR(PRINTER_OUT_PWR_N);
            PRU_OUT_SET(PRINTER_OUT_PAPER_SENSE);
            __delay_cycles(DELAY_100_MS);
            // Initialize the stepper motor. In case the initialization fails we
            // are going to end the print job right away.
            if (!initMotor()) {
                endJob = true;
            }
            break;
        case PRINTER_CMD_PRINT_LINE:
            // Before printing the line do a sanity check on the supplied print
            // data to make sure is exactly as long as we expect. This safety
            // mechanism could potentially save us from printing a bunch of
            // garbage.
            if (currentItem->length == PRINTER_BYTES_PER_LINE) {
                printLine((uint8_t *)currentItem->data);
            }
            break;
        case PRINTER_CMD_MOTOR_HALF_STEP:
            // Before advancing the paper do a sanity check that the payload
            // size field denoting how far to advance has the proper size, and
            // also limit the paper advance to a reasonable default. This may
            // save us from wasting a bunch of paper under certain erroneous
            // operating conditions. Furthermore, in case we encounter an error
            // we will stop the print job.
            if (currentItem->length == sizeof(uint32_t)) {
                uint32_t numberOfHalfSteps = (currentItem->data)[0];
                if (numberOfHalfSteps <= PRINTER_MAX_NR_HALF_STEPS) {
                    uint32_t i;
                    for (i = 0; i < numberOfHalfSteps; i++) {
                        if (!advanceMotorHalfStep()) {
                            endJob = true;
                        }
                    }
                }
                else {
                    // The host tried to issue a step command with a parameter
                    // that was too large. Be a good citizen and report an error
                    // back rather than to just silently ignore the command.
                    queue.status.bits.illegalParameterError = true;
                }
            }
            break;
        case PRINTER_CMD_TEST_SIGNALS:
            // Repeatedly send out the signal test vector. Note that this
            // function will never return.
            testPrinterOutputSignals();
            break;
        case PRINTER_CMD_CLOSE:
            // Wait a short moment to prevent glitching and then turn off the
            // stepper motor completely
            __delay_cycles(DELAY_5_MS);
            initMotor();
            // Turn off the end-of-paper sensor supply and the printer head
            // control logic
            PRU_OUT_CLR(PRINTER_OUT_PAPER_SENSE);
            PRU_OUT_SET(PRINTER_OUT_PWR_N);
            break;
        case PRINTER_CMD_REQUEST_PRU_HALT:
            // The host has requested a shut-down of the PRU after this print
            // job. Set a status flag that will get processed once we are
            // through with the print job.
            queue.status.bits.pruHaltRequested = true;
            break;
        case PRINTER_CMD_EOS:
            // Exit the print job processing loop
            endJob = true;
            break;
        default:
            // We should not get here. Exit the print job processing loop.
            queue.status.bits.illegalCommandError = true;
            endJob = true;
        }

        if (!endJob) {
            // Advance to the next item in the print job. This is done by moving
            // the pointer across the static command and length fields of the
            // current print job item and then further moving it over all of its
            // associated payload (if any).
            currentItem = (PRINTER_JobItem *)((uint8_t *)currentItem +
                    2 * sizeof(uint32_t) + currentItem->length);
        }
    }
}

static void printLine(const uint8_t dotData[]) {
    uint8_t byteIndex;
    uint8_t bitValue;
    uint16_t blackDotCounter = 0;

    // Iterate through all bytes in one line
    for (byteIndex = 0; byteIndex < PRINTER_BYTES_PER_LINE; byteIndex++) {
        // Iterate through all bits in each pixel-data byte
        for (bitValue = 0x80; bitValue != 0x00; bitValue >>= 1) {
            // Set the serial data output in case the pixel is set
            if (dotData[byteIndex] & bitValue) {
                // Ensure we don't print more than the maximum number of black
                // dots allowed for a line. This is a safety precaution to
                // prevent potential excess current flow in case of program
                // errors. The MPU code should never pass us a line with more
                // black dots than what is allowed.
                if (++blackDotCounter <= PRINTER_MAX_BLACK_DOTS_PER_LINE) {
                    PRU_OUT_SET(PRINTER_OUT_MOSI);
                }
                else {
                    // We stopped outputting black dots - this is an error
                    // condition. We should never get here-- only if the host
                    // hasn't properly pre-processed and partitioned the print
                    // job data.
                    queue.status.bits.tooManyBlackDotsError = true;
                    // Ensure that no more black dots will be output
                    PRU_OUT_CLR(PRINTER_OUT_MOSI);
                }
            }
            else {
                PRU_OUT_CLR(PRINTER_OUT_MOSI);
            }

            // Wait the necessary data setup time or clock width low time -
            // whichever is greater.
            __delay_cycles(MAX(DELAY_TSETUP_DI, DELAY_TW_CLK));

            // Generate one clock pulse and wait the required hold time or
            // clock width high time - whichever is greater.
            PRU_OUT_SET(PRINTER_OUT_CLK);
            __delay_cycles(MAX(DELAY_THOLD_DI, DELAY_TW_CLK));
            PRU_OUT_CLR(PRINTER_OUT_CLK);
        }
    }

    // Toggle the latch signal to accept the serial data into the printer head
    // internal buffer.
    __delay_cycles(DELAY_TSETUP_LAT);
    PRU_OUT_CLR(PRINTER_OUT_LAT_N);
    __delay_cycles(DELAY_TW_LAT);
    PRU_OUT_SET(PRINTER_OUT_LAT_N);
    __delay_cycles(DELAY_THOLD_LAT);

    // Toggle all strobe signals, one after another. This will actually print
    // the image. There is some room for optimization here to intelligently only
    // toggle the strobe lines that have actual black dots in their associated
    // sections.
    printerStrobe(PRINTER_OUT_STB1_N);
    printerStrobe(PRINTER_OUT_STB23_N);
    printerStrobe(PRINTER_OUT_STB4_N);
    printerStrobe(PRINTER_OUT_STB56_N);
}

static void printerStrobe(const uint32_t strobeSignal) {
    // wait the setup time for the strobe signal
    __delay_cycles(DELAY_TSETUP_STB);

    // Toggle the desired strobe line and wait the associated data out delay
    // time as well as the required strobe time.
    PRU_OUT_CLR(strobeSignal);
    __delay_cycles(MAX(DELAY_TD0, DELAY_STB));
    PRU_OUT_SET(strobeSignal);

    // Wait the driver out delay time
    __delay_cycles(DELAY_TD1);
}

static bool initMotor(void) {
    PRU_OUT_CLR(PRINTER_OUT_A1 | PRINTER_OUT_A2 | PRINTER_OUT_B1 | PRINTER_OUT_B2);
    motorStepIndex = 0;

#ifdef PRINTER_USE_THERMAL_SENSOR
    if (checkThermalAlarm()) {
        queue.status.bits.thermalAlarmError = true;
        return false;
    }
#endif

    // Set initial stepper motor delay. That's important to do here since we
    // rely on this event as we enter advanceMotorHalfStep() for the first time
    // later on.
    setIepCompareEvent0(DELAY_HALF_STEP);

    return true;
}

// http://www.nmbtc.com/step-motors/engineering/full-half-and-microstepping.html
static bool advanceMotorHalfStep(void) {
    const uint32_t phaseTable[8] = {
            PRINTER_OUT_A1,
            PRINTER_OUT_A1 | PRINTER_OUT_B1,
            PRINTER_OUT_B1,
            PRINTER_OUT_B1 | PRINTER_OUT_A2,
            PRINTER_OUT_A2,
            PRINTER_OUT_A2 | PRINTER_OUT_B2,
            PRINTER_OUT_B2,
            PRINTER_OUT_B2 | PRINTER_OUT_A1
    };
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

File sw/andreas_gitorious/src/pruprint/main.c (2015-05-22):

/*
 * main.c
 *
 * AM335x PRU-based Thermal Printer Demo Application
 *
 * This is a command line program that takes a PNG image, processes and slices
 * it into a print job suitable for the associated low-level PRU thermal printer
 * firmware, and then kicks off the printing of the image. The program also
 * offers various test and control functions that can be invoked by using
 * command line options. See the program's usage info for additional info.
 *
 * Written by Andreas Dannenberg, 01/01/2014
 *
 * Copyright (C) 2014 Texas Instruments Incorporated - http://www.ti.com/
 * ALL RIGHTS RESERVED
 */

#include <stdio.h>
#include <stdlib.h>
#include <string.h>
#include <stdint.h>
#include <stdbool.h>
#include <sys/time.h>
#include <png.h>

// PRU driver header file
#include "prussdrv.h"
#include "pruss_intc_mapping.h"

// Interface to the PRU-based printer driver firmware "pruprinter_fw"
#include "pruprinter.h"

// Include the generated PRU firmware from the "pruprinter_fw" project by
// including the associated header files.
#include "pruprinter_fw_iram.h"
#include "pruprinter_fw_dram.h"

#define USAGE_STRING                                                    \
    "Usage: %s [OPTION]... FILE\n"                                      \
    "       %s -f COUNT\n"                                              \
    "       %s -t\n"                                                    \
    "Prints the PNG image FILE using the PRU printer\n"                 \
    "\n"                                                                \
    "  -s START     First image row to print\n"                         \
    "  -e END       Last image row to print\n"                          \
    "  -i           Invert image while printing\n"                      \
    "  -f COUNT     Feed printer paper\n"                               \
    "  -t           Test pattern signal generation\n"                   \
    "               CAUTION: USE ONLY WITH NO PRINTER HW CONNECTED!\n"  \
    "  -w           Wait for ENTER before disabling PRU and exiting program\n"

// Global variable pointing to the printer queue that is located in the PRU
// shared memory section
static PRINTER_Queue *queue;

// Global variable pointing to the next job item in the printer queue that needs
// to be processed.
static PRINTER_JobItem *jobItem;

// Global variable pointing to the last valid memory location for job items
static void *jobItemsMaxAddress;

// Global variables for working with the image that was loaded
static uint32_t pngImageWidth, pngImageHeight;
static png_bytep *pngImageRowPointers;

// Function prototypes
static bool initPru(void);
static void disablePru(void);
static bool readPngImage(const char *fileName);
static void deallocPngImage(void);
static void initQueueJobItems(void);
static bool queueHasJobItems(void);
static void addJobItemToQueue(const uint32_t command, const uint32_t length,
        const uint8_t data[]);
static bool addJobItemToQueueLowLevel(const uint32_t command,
        const uint32_t length, const uint8_t data[]);
static void printImage(const uint32_t startLine, const uint32_t endLine,
        const bool inverse, const uint32_t paperFeedCountAfterPrint);
static void partitionLineAndPrint(const uint8_t dotData[],
        const uint16_t length, const bool inverse);
void measureDurationPrintToConsole(bool start);
void checkForPrinterErrorsPrintToConsole(void);

// Main Linux program entry point
int main(int argc, char *argv[]) {
    int opt;
    bool testFlag = false;
    bool paperFeedFlag = false;
    uint32_t paperFeedCount = 0;
    bool startLineFlag = false;
    uint32_t startLine = 0;
    bool endLineFlag = false;
    uint32_t endLine = 0;
    bool inverseFlag = false;
    bool waitFlag = false;

    // Parse the command line options and issue a simple help text in case
    // things don't match up. The columns behind the options denote that option
    // requires an argument. See getopt(3) for more info.
    while ((opt = getopt(argc, argv, "tf:s:e:iw")) != -1) {
        switch (opt) {
        case 't':
            testFlag = true;
            break;
        case 'f':
            paperFeedCount = atoi(optarg);
            paperFeedFlag = true;
            break;
        case 's':
            startLine = atoi(optarg);
            startLineFlag = true;
            break;
        case 'e':
            endLine = atoi(optarg);
            endLineFlag = true;
            break;
        case 'i':
            inverseFlag = true;
            break;
        case 'w':
            waitFlag = true;
            break;
        default:
            // getopt() will return '?' in case of a malformed command line in
            // which case we are printing the usage and exit the command.
            fprintf(stderr, USAGE_STRING, argv[0], argv[0], argv[0]);
            return EXIT_FAILURE;
        }
    }

    // Initialize the PRU and exit the program if that fails. Any errors that
    // may occur during that process will be output from within that function.
    if (!initPru()) {
        return EXIT_FAILURE;
    }

    // See if the test mode has been activated. If that's the case we will just
    // enter test mode right away.
    if (testFlag) {
        // Create a very simple print job that activates the test pattern
        // generation. Since this sub-function doesn't return within the PRU
        // firmware we don't need to bother trying to issue a halt command.
        initQueueJobItems();
        addJobItemToQueue(PRINTER_CMD_TEST_SIGNALS, 0, NULL);
        addJobItemToQueue(PRINTER_CMD_EOS, 0, NULL);

        // The interrupt is mapped via INTC to channel 1
        printf("Starting PRU GPIO test pattern generation\n");
        prussdrv_pru_send_event(ARM_PRU1_INTERRUPT);
    }
    // See if the paper feed flag has been set AND no image filename was given.
    // Unlike other print-related flags we want to allow the user to feed paper
    // without needing to specify an image to print.
    else if (paperFeedFlag && (optind >= argc)) {
        // Go ahead and create a very simple print job that simply feeds the
        // paper by the specified number of steps. Any other print-related
        // command line option will be ignored.
        initQueueJobItems();
        addJobItemToQueue(PRINTER_CMD_OPEN, 0, NULL);
        addJobItemToQueue(PRINTER_CMD_MOTOR_HALF_STEP, sizeof(uint32_t),
                (const uint8_t *)&paperFeedCount);
        addJobItemToQueue(PRINTER_CMD_CLOSE, 0, NULL);
        addJobItemToQueue(PRINTER_CMD_REQUEST_PRU_HALT, 0, NULL);
        addJobItemToQueue(PRINTER_CMD_EOS, 0, NULL);

        // The interrupt is mapped via INTC to channel 1
        printf("Start feeding paper\n");
        prussdrv_pru_send_event(ARM_PRU1_INTERRUPT);
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

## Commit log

2015-03-02 Added print head docs and sample schematic.
2015-03-06 Added print head image.
2015-04-15 Switched to Jekyll project page
2015-05-06 Added docs and hw
    [526100833.stp, 526103033.stp, AM335x_Thermal_Printer.PcbDoc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]
2015-05-06 Generated DRV8833 libraries
    [DRV8833_PWP_16.PcbLib, DRV8833_PWP_16.SchLib, PWP0016A.stp]
2015-05-06 Added motor driver libs
    [AM335x_Thermal_Printer.PrjPCB, AM335x_Thermal_Printer.SchDoc]
2015-05-07 Added libs for LM393 and SN74LVC244A
    [LM393_DGK_8.PcbLib, LM393_DGK_8.SchLib, LM393_DGK_8_DGK0008A.stp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]
2015-05-08 Added docs and libs
    [541324062.stp, AM335x_Thermal_Printer.PcbLib, AM335x_Thermal_Printer.SchDoc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]
2015-05-09 Added BBB libs
    [AM335x_Thermal_Printer.PcbLib, AM335x_Thermal_Printer.SchDoc, AM335x_Thermal_Printer.SchLib]
2015-05-12 Organized PRU signals
    [AM335x_Thermal_Printer.SchDoc, TPCape_RevA_BOM.xlsx]
2015-05-13 Added FPC interface board mapping xls
    [AM335x_Thermal_Printer.SchDoc, TPCape_RevA_BOM.xlsx]
2015-05-14 3 versions init commit
    [DRV8833_PWP_16.SchLib, TPCape_RevA_BOM.xlsx, TPcape_basic.PcbDoc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]
2015-05-14 updated thermal printer notes
2015-05-14 Added motor driver
    [AM335x_Thermal_Printer.SchLib, DRV8833_PWP_16.SchLib, TPCape_RevA_BOM.xlsx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]
2015-05-15 Added EEPROM and power research
    [AM335x_Thermal_Printer.PcbLib, AM335x_Thermal_Printer.SchLib, TPCape_RevA_BOM.xlsx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]
2015-05-15 Assigned buffers and added drv8833c libs
    [DRV8833C_HTSSOP.PcbLib, DRV8833C_HTSSOP.SchLib, PW0020A.stp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]
2015-05-16 Added external pulls and decaps
    [AM335x_Thermal_Printer.SchDoc, AM335x_Thermal_Printer.SchLib, TPCape_RevA_BOM.xlsx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]
2015-05-17 Added schematic notes
    [TPcape_basic.SchDoc]
2015-05-17 Added power libs, silk base images, ultra
    [2015-05-17_13-58-061.schdoc, BEAGLEBONEBLACK_REV A5B.PrjPcb, BEAGLEBONEBLACK_REV A5B.SCHLIB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]
2015-05-18 Added photo transistor comparator circuit
    [TPCape_RevA_BOM.xlsx, TPcape_basic.PrjPCB, TPcape_basic.SchDoc]
2015-05-18 Edited thermister circuit
    [TPcape_basic.SchDoc]
2015-05-19 Added LM393 comparator libs
    [LM339_PW_14_PW0014A.stp, LM393_D_8.PcbLib, LM393_D_8.SchLib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]
2015-05-20 Added LM393 TSSOP pcb libs
    [LM393_PW_8.PcbLib, LM393_PW_8.SchLib, LM393_PW_8_PW0008A.stp]
2015-05-21 Playing with mosfet circuit
    [TPcape_basic.SchDoc]
2015-05-21 Added power circuit, cleaned up comparator docs
    [AM335x_Thermal_Printer.PcbLib, AM335x_Thermal_Printer.SchLib, LM339_PW_14_PW0014A.stp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]
2015-05-21 Added LM393 DGK libs
    [LM393_DGK_8.SchLib, TPcape_basic.PrjPCB, TPcape_basic.SchDoc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]
2015-05-21 Cleaned up sensor circuit
    [TPcape_basic.SchDoc]
2015-05-22 Added Paul's comments to sch and copied over Andreas' project
    [TPcape_basic.SchDoc]
2015-05-22 Added new power solution and watchdog component libs
    [TPS3126E12_DBV0005A.stp, TPS3126E12_DBV_5.PcbLib, TPS3126E12_DBV_5.SchLib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]
2015-06-16 Added sw and updated with latest design files. Updated README
    [DRV8833_PWP_16.PcbLib, DRV8833_PWP_16.SchLib, PWP0016A.stp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]
2015-06-18 Added TPcape_breakout PCB
    [AM335x_Thermal_Printer.PcbLib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]
2015-08-03 Added TPcape breakout board assembly images.
